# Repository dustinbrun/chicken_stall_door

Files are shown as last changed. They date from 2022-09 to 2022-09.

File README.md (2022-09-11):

# Arduino electric chicken stall door
Diy motorized door for a chicken stall, controlled by Arduino Nano

# Features
- motor can be controlled with
  - buttons on the main controller box
  - 433 Mhz remote
  - UART (RX/TX) communication (can be used with a PC or with a ESP8266 to make the system controllable over Wifi)
- two Reed-switches to indicate top and bottom position of the door
- safety end-stop-switch to cut off the power if the door in case of failure does not stop in its top position
- Solenoid lock to lock the door
- leds to indicate error/ready state

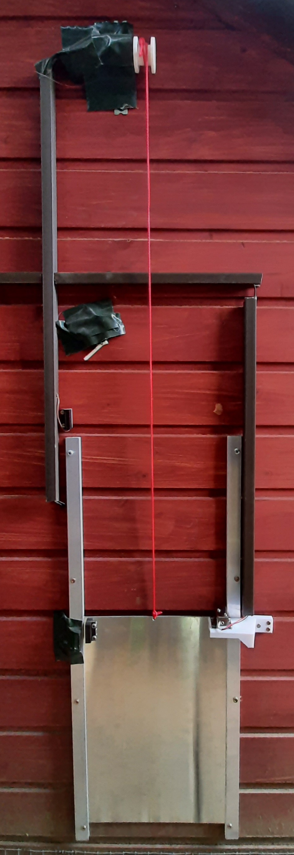
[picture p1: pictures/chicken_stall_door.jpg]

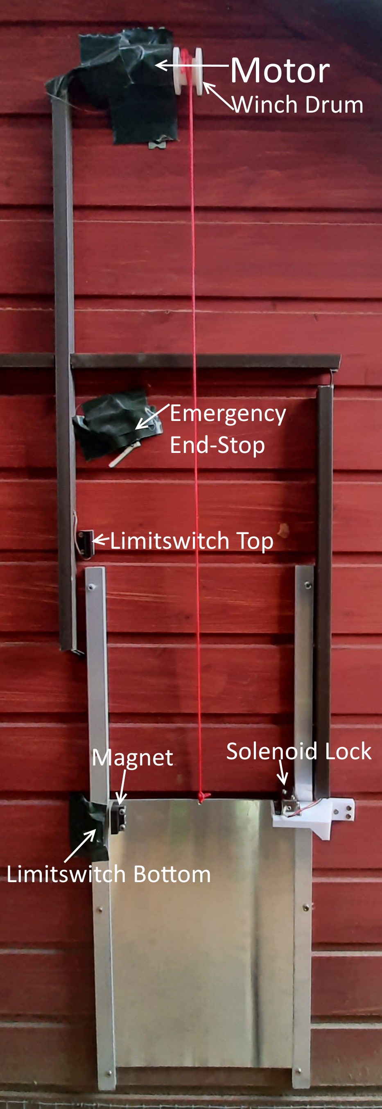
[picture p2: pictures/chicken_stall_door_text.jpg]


# Hardware

## Parts-List
- Motor with gear-system to create some holding torque in the top position (and stop the door from going down again by itself).
  I used one with 20 rpm and a torque of 0,15Nm ([link](https://www.pollin.de/p/gleichstrom-getriebemotor-pgm-37dc12-21-310482))
- HG7881 motor driver board, I used this one ([link](https://www.pollin.de/p/motorantriebsmodul-daypower-motor-9110-810572))
  
  OR: A [TLE4202B](https://www.pollin.de/p/tle4202b-sts-b57928-101044) and a N-Channel Mosfet to create your own motor- and solenoid-driver board (see below)
- 2x Some kind of door reed contact ([link](https://www.pollin.de/p/tuerkontakt-fensterkontakt-mit-25-cm-anschlusslitzen-10-w-braun-580569))
- 433 Mhz receiver ([link](https://www.amazon.de/iHaosapce-Wireless-Transmitter-Receiver-Raspberry/dp/B07B9KV8D9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))

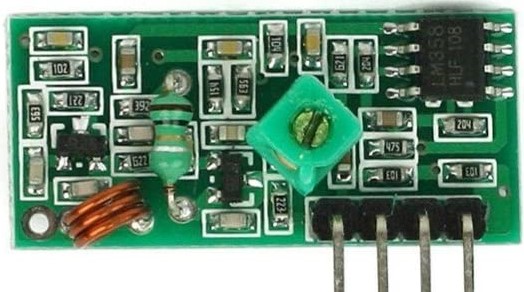
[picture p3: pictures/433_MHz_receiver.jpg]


- Solenoid Lock ([link](https://www.ebay.de/itm/273873875970), 12V/350mA version)
- Some leds, resistors, screw terminals, ...

## Schematic
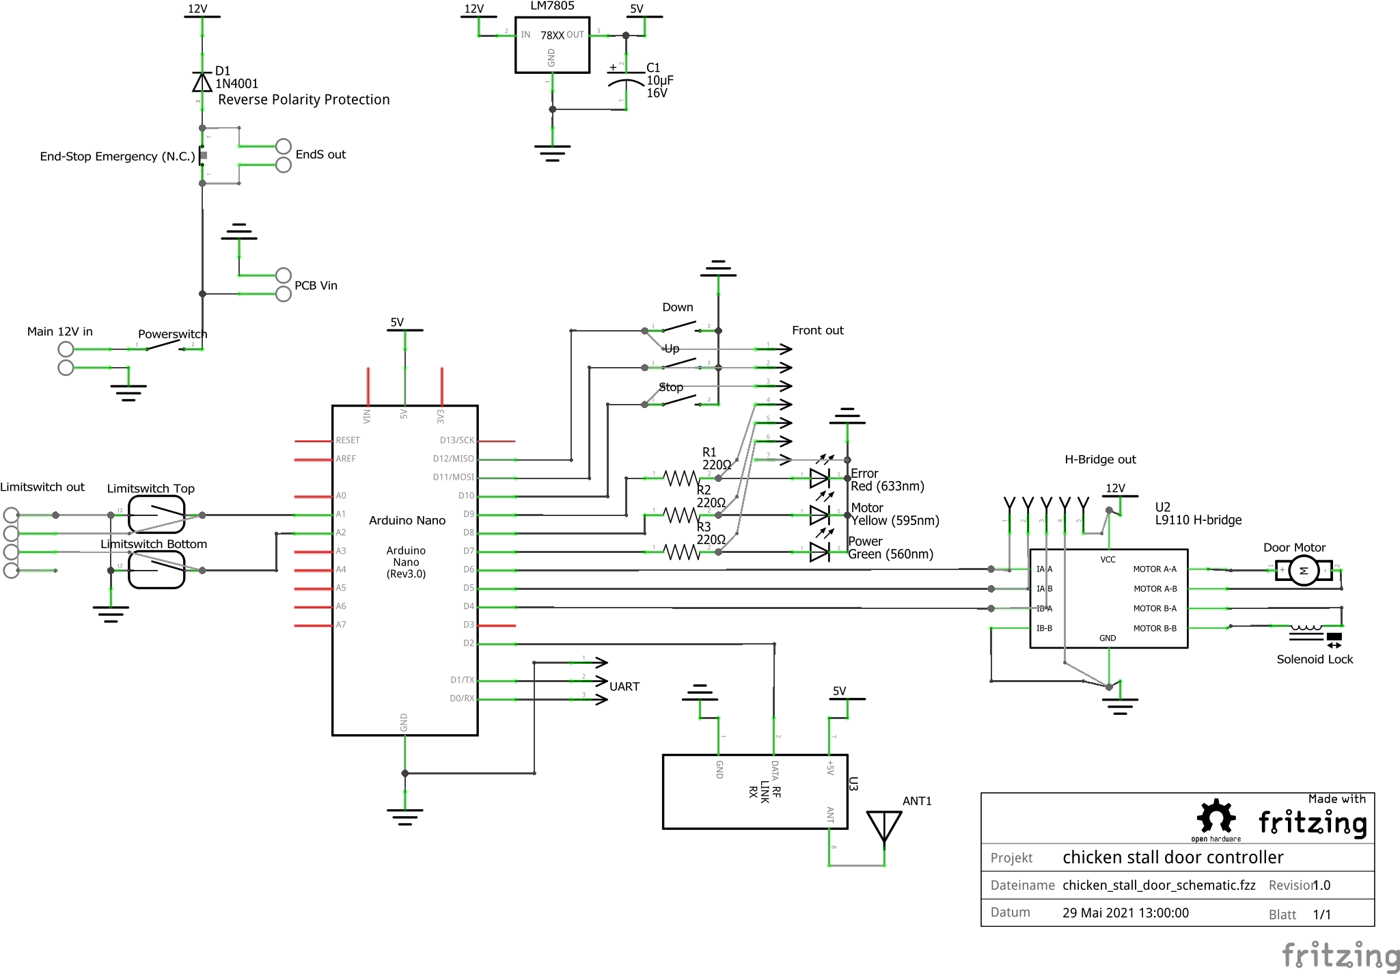
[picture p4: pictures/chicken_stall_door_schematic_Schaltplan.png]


## PCB Layout
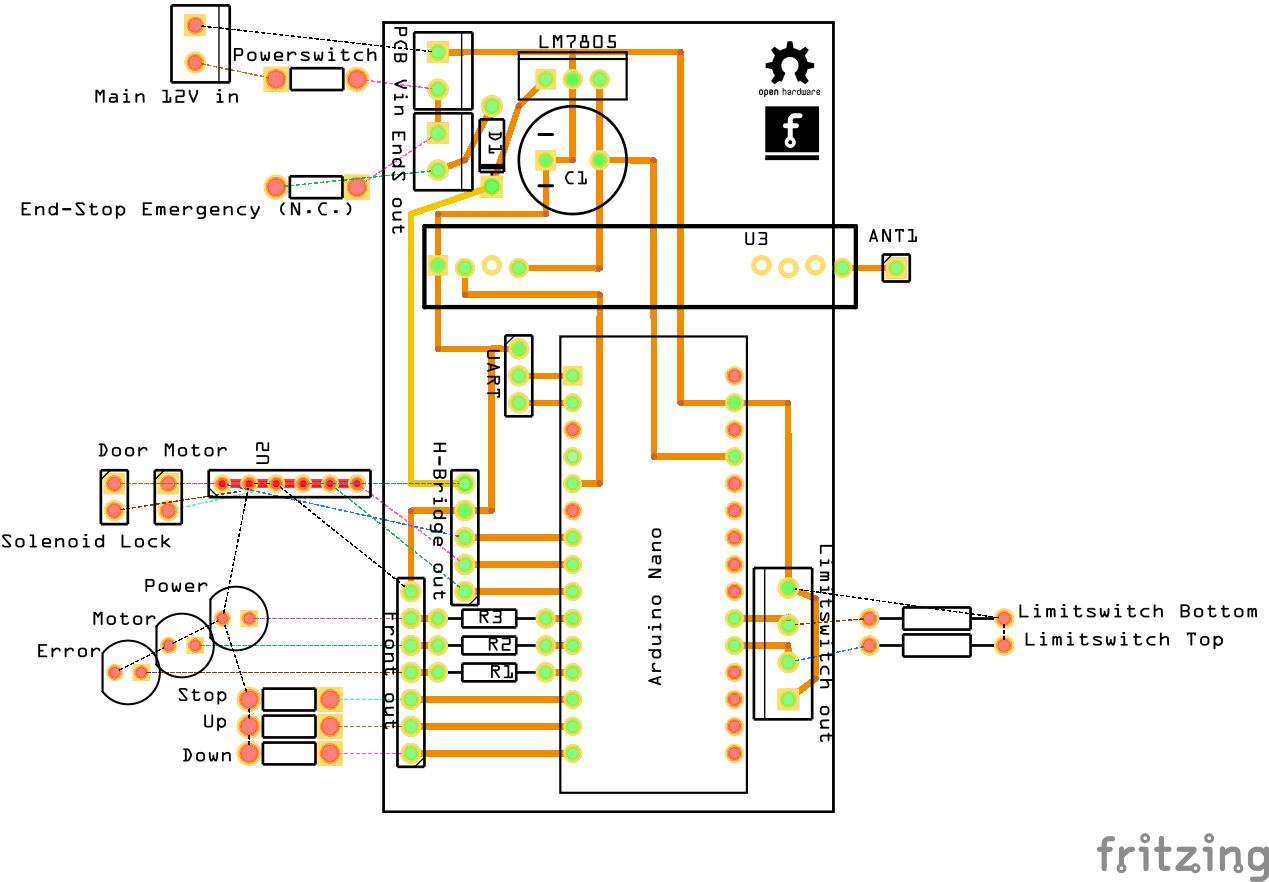
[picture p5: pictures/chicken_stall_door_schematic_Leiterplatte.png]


## Front panel for the main controller
The size of this frontpanel is 125x70mm. You can customize it using the free ["Frontplatten Designer"](https://www.schaeffer-ag.de/frontplatten-designer).

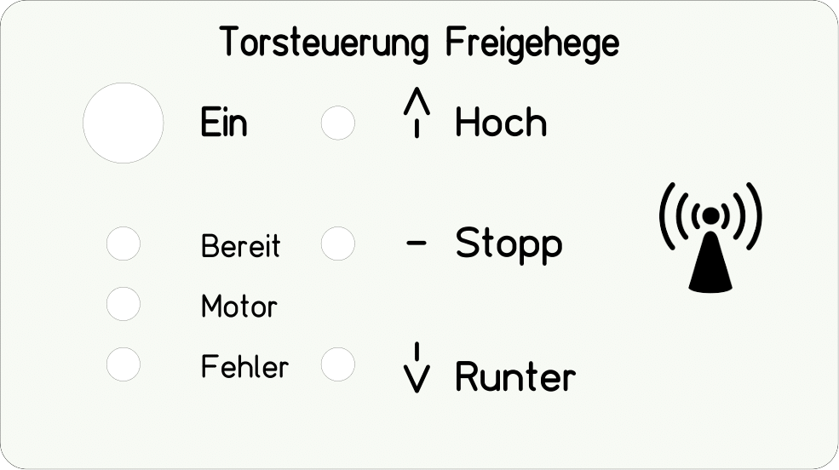
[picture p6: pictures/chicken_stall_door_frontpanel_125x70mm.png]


# Motor Driver
You can either use a premade motor driver like the one I linked in the parts list or build your own. The pins on the main pcb for this driver stay the same.
This driver is based on the TLE4202B. Since the solenoid lock doesn’t need a in the polarity switchable voltage, we can use a simple Mosfet to control it.

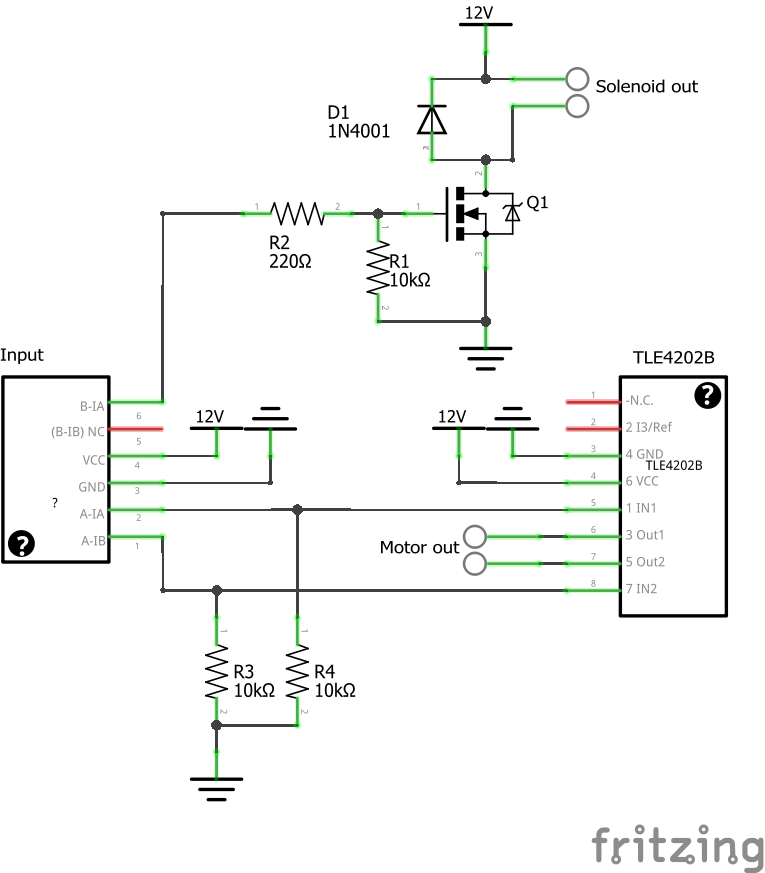
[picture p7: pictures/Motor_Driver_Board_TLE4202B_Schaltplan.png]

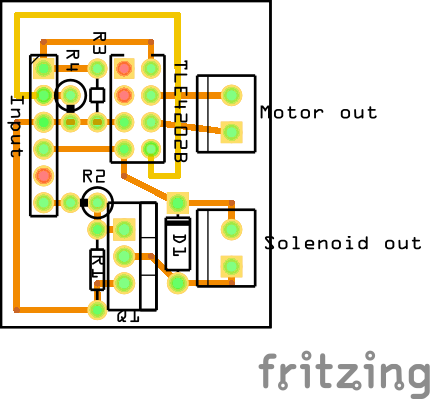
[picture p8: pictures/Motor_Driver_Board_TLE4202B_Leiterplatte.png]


This circuit is not perfect, since it does not feature any filter-capacitors, which are recommended in the datasheet. But it works for the most parts :).

# 3D-printed parts
## Winch drum for the motor
I created a 3D-model for a winch drum, to which rope of the door the can be spooled to. It fits to the flattened motor axis. A M3 screw can be screwed in the second hole to tighten the motor axis. The rope can also be tightened to this screw (if the screw is long enough). This part fits to the motor linked in the parts list and I think it will also fit to any other motor with 6mm axis.
You can customize the model using tinkercad and [this link](https://www.tinkercad.com/things/7C84V8nsqCm).
### [3D-Model](Motor_Winch_Drum.stl)
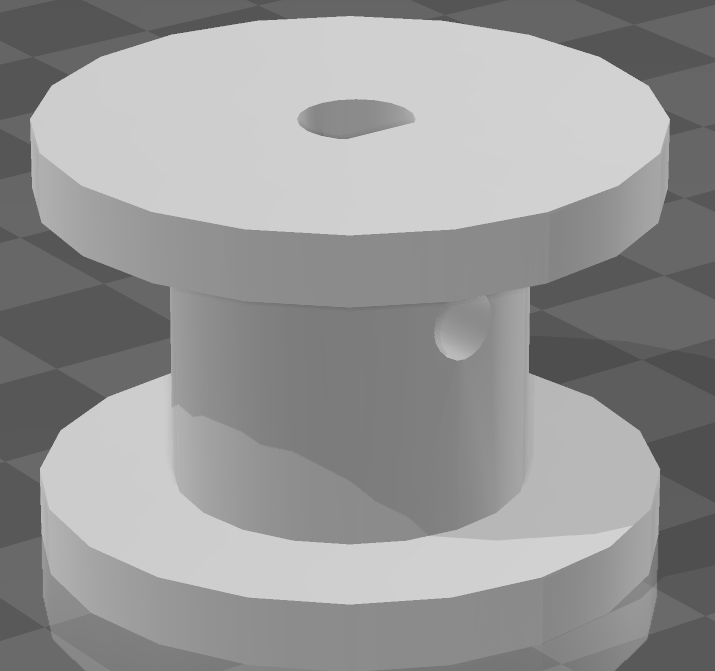
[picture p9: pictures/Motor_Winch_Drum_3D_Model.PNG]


## Mount for the solenoid lock
This part is used to hold the solenoid lock. It will fit to the solenoid linked in the parts list. For other solenoids please check the dimensions. You can customize the model using tinkercad and [this link](https://www.tinkercad.com/things/a6mTNkn8J4k).
### [3D-Model](Solenoid_Lock_Mount.stl)
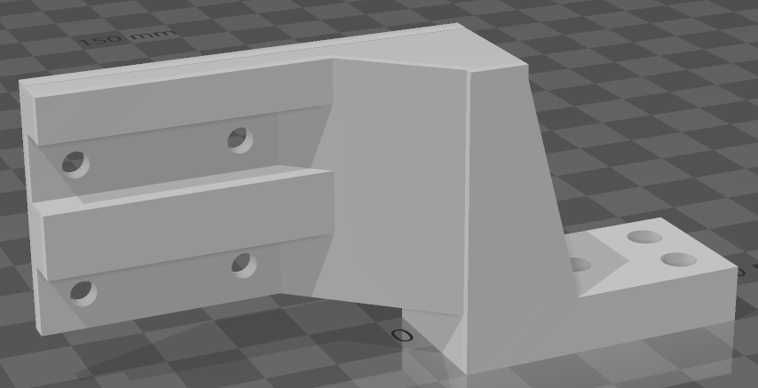
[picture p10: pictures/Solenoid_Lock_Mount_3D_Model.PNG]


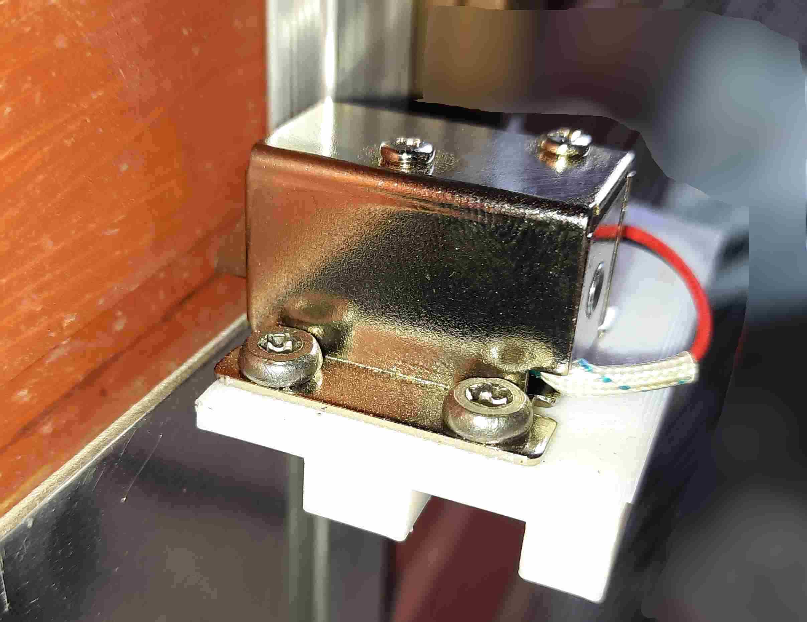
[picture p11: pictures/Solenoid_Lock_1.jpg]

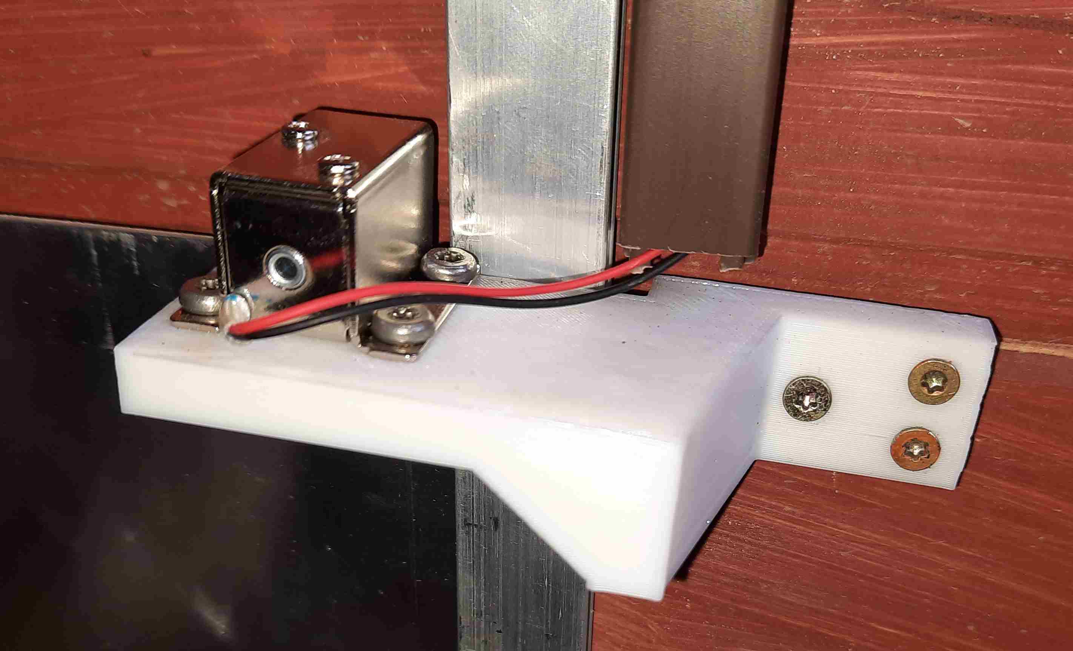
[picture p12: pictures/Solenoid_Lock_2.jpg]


# Software
In the code I am using the RCSwitch-library. Since it is already included in the code-folder there is no need to download an import it manually. I have linked it in the code anyway.

To get your 433Mhz remote working with the controller fist upload the `ReceiveDemo_Simple.ino`-sketch from the RCSwitch-Library examples. Now open the serial monitor an then press the keys on your remote, that you want to use. Now copy the received codes from the serial monitor into the `Remote Codes`-Section in the code.

You need to test out how long your opening/closing process of the door takes with your motor. If you have measured it add a few seconds to the value an change the `motor_timeout`-variable in the code to this value in **milliseconds** (10s = 10000ms). If the motor is running longer than this timeout it stops automatically.

## Serial Communication
I implemented a serial interface to control the movement. If you add a Wifi-capable microcontroller (like the ESP8266) to this interface, it can make the system remote-controllable over wifi.

The functionality of the UART interface:
- Baudrate: **9600**
Commands:
- Request State of the Door: 'S'
  - Returns: 1 - Door is open, 0 - Door is closed, 2 - Unknown Position
- Open Door: 'U'
  - Returns: 'U'
  - If it fails or not possible (already open): 'E'
- Open Door: 'D'
  - Returns: 'D'
  - If it fails or not possible (already closed): 'E'
- Stop Movement: 'H'
  - Returns: 'H'

# References/Sources
- RC Switch Lib: https://github.com/sui77/rc-switch
- CCC - Chicken-Coop-Control: https://sites.google.com/view/arduino-chicken-coop-control/home
- https://funduino.de/nr-03-433mhz-funkverbindung

<br>
<p xmlns:dct="http://purl.org/dc/terms/" xmlns:cc="http://creativecommons.org/ns#" class="license-text">This work by <span property="cc:attributionName">Dustin Brunner</span> is licensed under <a rel="license" href="https://creativecommons.org/licenses/by/4.0">CC BY 4.0</a></p>

<br />Dieses Werk von <span xmlns:cc="http://creativecommons.org/ns#" property="cc:attributionName">Dustin Brunner</span> ist lizenziert unter einer <a rel="license" href="http://creativecommons.org/licenses/by/4.0/">Creative Commons Namensnennung 4.0 International Lizenz</a>.

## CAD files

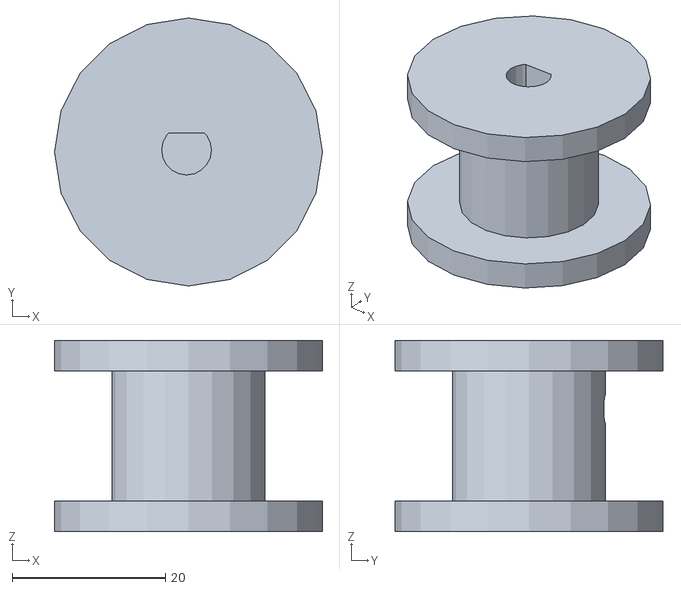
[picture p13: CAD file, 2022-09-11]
Motor_Winch_Drum.stl
35.0 x 35.0 x 25.0

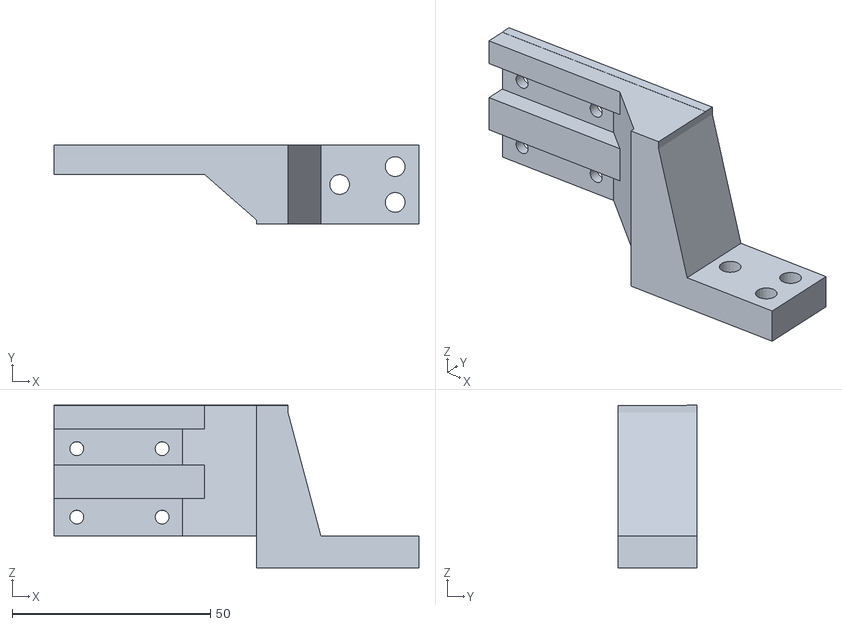
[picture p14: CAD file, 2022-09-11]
Solenoid_Lock_Mount.stl
92.0 x 20.0 x 41.1

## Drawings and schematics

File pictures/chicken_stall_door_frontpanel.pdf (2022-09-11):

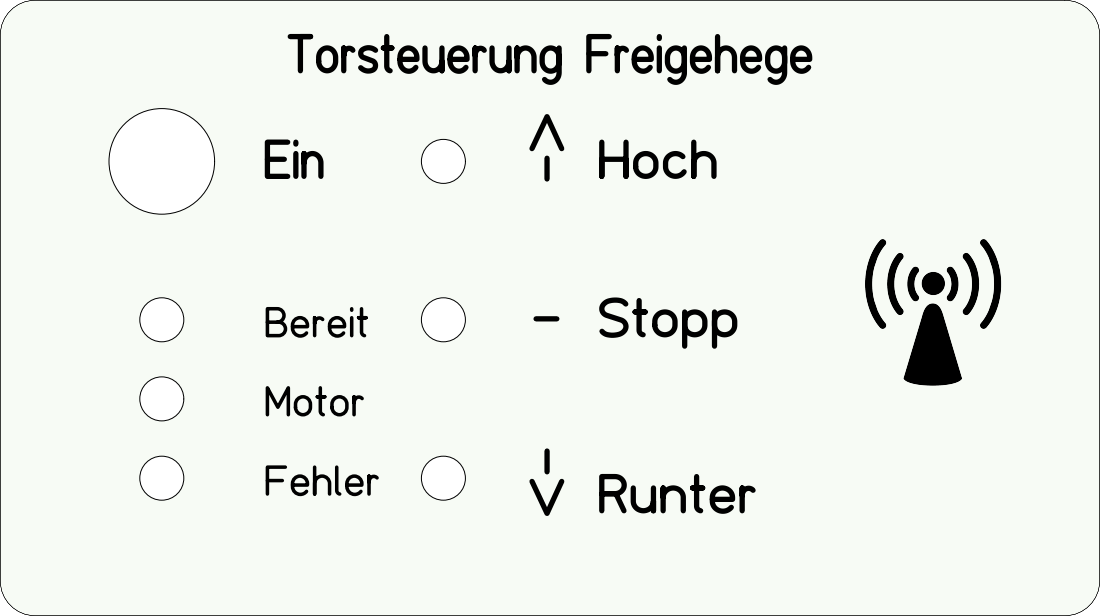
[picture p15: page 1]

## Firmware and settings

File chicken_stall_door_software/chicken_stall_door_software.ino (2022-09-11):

/*
   Hasenklappe
   Author: dustinbrun
           licensed under CC BY 4.0
   Version 09.2022

   Source 433Mhz Receiver: https://funduino.de/nr-03-433mhz-funkverbindung


   ------ Serial Communication, Baud: 9600 ------
   - Request State of the Door: 'S'
      - Returns: 1 - Door is open, 0 - Door is closed, 2 - Unknown Position
   - Open Door: 'U'
      - Returns: 'U'
      - If it fails or not possible (already open): 'E'
   - Open Door: 'D'
      - Returns: 'D'
      - If it fails or not possible (already closed): 'E'
   - Stop Movement: 'H'
      - Returns: 'H'

*/


#include "RCSwitch.h" // https://github.com/sui77/rc-switch

//Variables
int motor_timeout = 20000; //Motor stops after this limit (in ms) is reached, Maximum time for the Opening-/Closing- Process
int solenoid_on_time = 2000; //Time for the solenoid to be switched on (in ms) after the opening process was started. The door should exceed the solenoid position within this interval

//Remote Codes
long int remote_code_up = 5592512;  //Received Remote Codes, to which the Arduino reacts to, change to the Values of your remote. You can read those code using the "ReceiveDemo_Simple.ino"-code from the rc-switch Library
long int remote_code_down = 5592368;
long int remote_code_stop = 5592332;


// Pins
const int button_down = 12;
const int button_up = 11;
const int button_stop = 10;
const int led_error = 9;
const int led_motor = 8;
const int led_power = 7;
const int motor_a = 6;
const int motor_b = 5;
const int limit_top = A1;
const int limit_bottom = A2;
const int remote_interrupt_pin = 0; // Interrupt-Pin 0 = Arduino Pin D2
const int lock_pin = 4;


unsigned long motor_start_time = 0;
bool go_up = false;
bool go_down = false;
bool stop = false;

RCSwitch remote = RCSwitch();

void setup()
{
  Serial.begin(9600);
  remote.enableReceive(remote_interrupt_pin);

  pinMode(button_down, INPUT_PULLUP); //Pressed = LOW
  pinMode(button_up, INPUT_PULLUP);
  pinMode(button_stop, INPUT_PULLUP);
  pinMode(led_error, OUTPUT);
  pinMode(led_motor, OUTPUT);
  pinMode(led_power, OUTPUT);
  pinMode(motor_a, OUTPUT);
  pinMode(motor_b, OUTPUT);
  pinMode(lock_pin, OUTPUT);
  pinMode(limit_top, INPUT_PULLUP);   //Triggered = LOW
  pinMode(limit_bottom, INPUT_PULLUP);

  digitalWrite(motor_a, LOW);
  digitalWrite(motor_b, LOW);
  digitalWrite(lock_pin, LOW);
  digitalWrite(led_error, HIGH);
  digitalWrite(led_motor, HIGH);
  digitalWrite(led_power, HIGH);

  delay(200);
  digitalWrite(led_error, LOW);
  digitalWrite(led_motor, LOW);

  //Serial.print("A");
}

void loop()
{
  if ((digitalRead(button_down) == LOW || go_down) && digitalRead(limit_bottom) != LOW)
  {
    delay(100);
    stop = false;
    motor_start_time = millis();
    motor_down();

    while (digitalRead(limit_bottom) != LOW &&
           millis() - motor_start_time < motor_timeout &&
           stop != true)
    {
      check_messages();
      delay(10);
    }

    motor_stop();

    if ((millis() - motor_start_time >= motor_timeout) || stop == true)
    {
      digitalWrite(led_error, HIGH);
      Serial.print("E");
      delay(500);
      digitalWrite(led_error, LOW);
    }
    else
    {
      digitalWrite(led_error, LOW);
      Serial.print(get_pos());
    }

    go_down = false;
    stop = false;
    delay(200);
  }
  else if ((digitalRead(button_down) == LOW || go_down) && digitalRead(limit_bottom) == LOW)
  {
    digitalWrite(led_error, HIGH);
    Serial.print("E");
    delay(500);
    digitalWrite(led_error, LOW);
    go_down = false;

  }


  if ((digitalRead(button_up) == LOW || go_up) && digitalRead(limit_top) != LOW)
  {
    delay(100);
    stop = false;
    door_unlock();
    motor_start_time = millis();
    motor_up();

    while (digitalRead(limit_top) != LOW &&
           millis() - motor_start_time < motor_timeout &&
           stop != true)
    {
      check_messages();
      delay(10);
      if(millis() - motor_start_time > solenoid_on_time)
      {
          door_lock();
       }
    }

    motor_stop();
    door_lock();

    if ((millis() - motor_start_time >= motor_timeout) || stop == true)
    {
      digitalWrite(led_error, HIGH);
      Serial.print("E");
      delay(500);
      digitalWrite(led_error, LOW);
    }
    else
    {
      digitalWrite(led_error, LOW);
      Serial.print(get_pos());
    }

    go_up = false;
    stop = false;
    delay(200);
  }
  else if ((digitalRead(button_up) == LOW || go_up) && digitalRead(limit_top) == LOW)
  {
    digitalWrite(led_error, HIGH);
    Serial.print("E");
    delay(500);
    digitalWrite(led_error, LOW);
    go_up = false;

  }

  check_messages();
  delay(10);

}

void check_messages()
{
  if (Serial.available()) {
    char serial_message = Serial.read();
    led_power_blink();

    if (serial_message == 'S') // Get State
    {
      Serial.print(get_pos()); // 1 - Door is open, 0 - Door is closed, 2 - Unknown Position
    }
    else if (serial_message == 'U')
    {
      go_up = true;
      Serial.print("U");
    }
    else if (serial_message == 'D')
    {
      go_down = true;
      Serial.print("D");
    }
    else if (serial_message == 'H')
    {
      stop = true;
      Serial.print("H");
    }
  }

  if (remote.available())
  {
    long int remote_message = remote.getReceivedValue();
    led_power_blink();

    if (remote_message == remote_code_up)
    {
      go_up = true;
    }
    else if (remote_message == remote_code_down)
    {
      go_down = true;
    }
    else if (remote_message == remote_code_stop)
    {
      stop = true;
    }
    /*else // Unknown Code
      {
      digitalWrite(led_error, HIGH);
      Serial.print("E");
      delay(100);
      digitalWrite(led_error, LOW);
      }*/

    remote.resetAvailable();
  }

  if (digitalRead(button_stop) == LOW)
  {
    stop = true;
  }

}


int get_pos()
{
  if (digitalRead(limit_top) == LOW) return 1;
  else if (digitalRead(limit_bottom) == LOW) return 0;
  else return 2;
}


void motor_down()
{
  digitalWrite(led_motor, HIGH);
  digitalWrite(motor_a, LOW);    //Motor going down
  digitalWrite(motor_b, HIGH);
}
void motor_up()
{
  digitalWrite(led_motor, HIGH);
  digitalWrite(motor_a, HIGH);    //Motor going up
  digitalWrite(motor_b, LOW);
}
void motor_stop()
{
  digitalWrite(led_motor, LOW);
  digitalWrite(motor_a, LOW);    //Motor stop
  digitalWrite(motor_b, LOW);
}

void door_lock()  //Normally closed Solenoid Lock
{
  digitalWrite(lock_pin, LOW);
}
void door_unlock()
{
  digitalWrite(led_motor, HIGH);
  digitalWrite(lock_pin, HIGH);
  delay(200);
  digitalWrite(led_motor, LOW);
  delay(200);
}

void led_power_blink()
{
  digitalWrite(led_power, LOW);
  delay(50);
  digitalWrite(led_power, HIGH);
}
